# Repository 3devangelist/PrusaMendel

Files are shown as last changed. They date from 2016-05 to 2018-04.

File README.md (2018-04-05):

WARNING: This file is a work in progress and may contain one or two orthographic errors... or maybe more!

# maZEmendel

<p align="center">
  
</p>

I have made this because I can, and i love history! and is a historic printer!

My motivation is to make a printer with a printer, i have a [*Beethefirst+*](https://beeverycreative.com/beethefirstplus/), that is **portable** and **user friendly** and I wanted to prove that with a Little machine, I could create a bigger one! and more maker oriented.
That is the base of REPRAP movement!

You will have all the gcode already generated to print one just like mine in you beethefirst! and if you do, **Show me!**

## First technical notes about this printer

This printer is not easy to assemble, It has a lot of bolts and hardware, but if well assembled, it can be reliable.
You have a calibration paragraph, as a guide for you to calibrate the perpendicularity of the X,Y and Z axis.
I have printed the majority of the parts in PETG because my BTF+ (beeverycreatrive printer) prints it very well, it is more flexible than PLA, thus absorbs some vibrations and has better layer adhesion.

**Side note** if you use PETG, try to use one that is transparent, the opaque ones normally has worse strength proprieties.

## Modeling
I have used **BLENDER**, because I'am a blender hardcore-user, because I can, and because it's really good to edit meshes.

To cut pieces, I have used Rhino, because it's the only paid CAD program i have, but you can use the dxf files, or send me a mail for me to convert the files to your format. To bee fair the only part you have to cut with precision is the Y wood base, later on, i will post the fabrication manual.

The file as called *"maise.blend"*, with that file i have rendered all images for the manual, and modeled all parts that I need to create or change for this build. If you need to edit it, you can and you should! That is the purpose of sharing the code. All the parts have the same name of the BOM file, and are distributed by layers, I know that it could be better organized, but better done than perfect.
You should use some add-on's like "3d print toolbox", "Layer management", "cycle engine", when you use models from blender you can try to clean all the mesh to be printable, but that is normally for power users, and when you use Boolean tools is impossible to make that without losing the modifiers stack, and we have to source the more editable parts we can, for others to be able to change. The pipe-line I use is export meshes to stl with "3d print toolbox" add on, then I use a tool that came with windows10 called "3d Builder" that is great to correct the meshes.

### Correcting meshes on 3d Builder

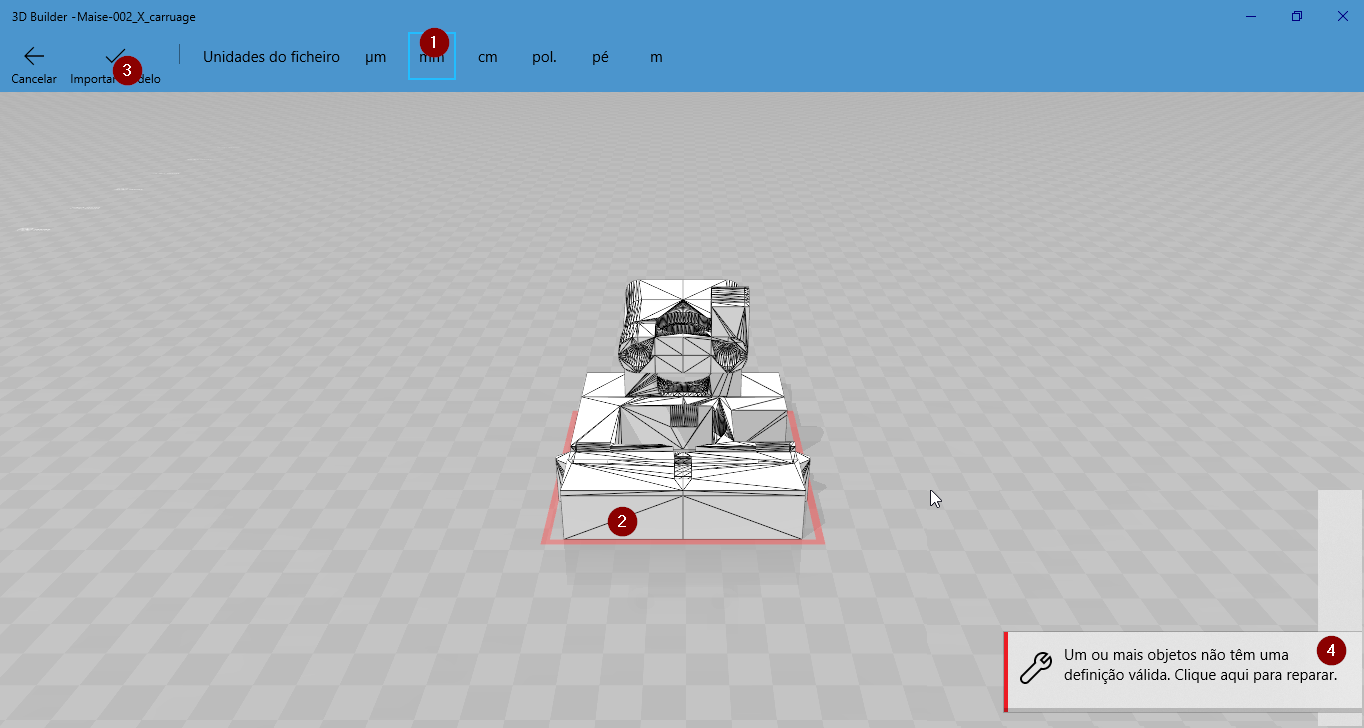
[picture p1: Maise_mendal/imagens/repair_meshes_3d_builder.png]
image 3d builder - heal meshes


- 1 Import as mm;
- 2 A red rectangle in the base of the model, means that the model has errors;
- 3 Import the model;
- 4 When you import the model, a rectangle shows up in the right down of your screen, click on it to repair;
- 5 Save your file em STL;

## Changes

- New X axes;
- remodeled Y;
- Some updates on Z;
- Bowden for extruder;
- E3d v6 hotend;
- Igus sliders for X and Y;
- board MKSgen 1.4;
- Drivers X, Y, E, Trynamic 2100, Z LV8729;
- Added LEDs to the system, you can add RGB "if you do show it!"

Working..

## BOM Build of Materials

[Spreedsheet](https://docs.google.com/spreadsheets/d/16tOSJMvPqgqwrDMo-RX5avmmjWwADpJSkYPEsrkDC4U/edit?usp=sharing)
(only parts to be printed the parts to buy needs to be updated)

## 1. Assembly the Printer

### 1.1. Structure
montage

1. Pick 6X380 M8 rods, and 2X *"001 bar-clamp-tall"*, and M8 Bolts and Washers, and displace them like in the picture.
2. Pick parts: **4X** *"001 Frame vertex with foot"*; **2X** *"001 frame-vertex"*, and assemble 2 strutures like on the image, tighten the nuts by hand. 
3. Pick 6X M8x40 Bolts and assemble like picture, to make shore that the frame will be the most simetric possible, like picture 4. then you can tighten a Little bit before brake, all the nuts.
4. The continuing of picture 3.
5. Pick the M8 Rods like is in the picture, and pick the **6X** *"001 bar-clamp"*, and assemble properly.
6. Assemble the main structure, by hand;

### 1.2. Y Axes

waiting for update

### 1.3. X Axes

waiting for update

### 1.4. Extruder

#### 1.4.1 Saintflint

<p align="center">
  
</p>

This is the best bowden printed extruder I have used! It was developed by a great friend [Michael Memeteau](https://incompreendido/in/mmemetea/), creative and resourceful engineer.
This extruder has a concept that double the area of contact between the motor gear and the filament.
I have edited the model to fit a MK10 type of gear if you have diferent requirements, feel free to edit, you have an editable file [onshape instance](https://cad.onshape.com/documents/5c209690b10748338481382a/w/6d6638f54420d7c76fe7949d/e/2d47f4694787414fab59244e)

In the [source](https://www.thingiverse.com/thing:979113) you have all information you need to assemble the extruder!

**Recommendation** - print all the parts in PETg and 90% infill, it takes longer, uses more plastic but it makes sure you din't end up with a broken extruder.

### 1.5. Hotend
I have used a Bowden setup with E3d v6 Chinese clone, before all the test I am thinking about upgrading it to an original one!

### 1.6. MKS GEN 1.4

I have chosen this because it has a good value for the money, in the BOM you have links to buy the board, Since I want a silent machine I decided to use the TMC2100 stepper drivers for the X, Y and E axis. They are not cheep but they are worth it!
You should be able to assemble the controller with these [instructions](http://reprap.org/wiki/MKS_GEN) from reprap community, if you use LEDs you should connect to the 12V output, the same place you connect the hotend fan.

#### 1.6.1. Assemble models with electronics

waiting for update

### 1.7. ATX Power supply 
To use a PC ATX power supply, you have to convert it, go to this [instructables](http://www.instructables.com/id/A-Makers-Guide-to-ATX-Power-Supplies/) you only need the 12V track, unless you config a raspberrypi with octaprint, if you do, use the 5x track to power the raspberrypi.

### 1.9 Filament Sensor

To implement!

## Firmware _**(Fernando to review)**_

I have a Firmware that you can use [here](https://github.com/3devangelist/PrusaMendel/tree/master/Maise_mendal/Firmware), if you want to configure yourself these Topic you should be able to implement with these [resources](http://marlinfw.org/docs/configuration/configuration.html).
For Base of the firmware i have on git, i have used the Marlin with the hephestos config files, and then edit it them.

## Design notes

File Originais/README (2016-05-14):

Prusa Mendel iteration 2

This is second big change, formerly known as felt branch.
Released 11.11.11 :-)

Please read http://reprap.org/wiki/Prusa_Mendel before attempting to build this. There is also PDF (manual-wiki) with backup documentation from reprap.org.  

Imported stuff:
Extruder by Greg Frost
Parametric Involute Bevel and Spur Gears by GregFrost
Belt pulley is http://www.thingiverse.com/thing:3104 by GilesBathgate

Prusa Mendel part list:

To print (not including the extruder drive):

4x frame-vertex-with-foot
2x frame-vertex-without-foot
2x coupling
1x x-carriage
1x x-end-idler
1x x-end-motor
2x z-motor-mount
4x belt-clamp
2x belt-clamp-nut-holder
8x bar-clamp
2x rod-clamp
1x y-motor-bracket
3x y-bushing
3x endstop-holder

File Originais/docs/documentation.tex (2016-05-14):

\documentclass[11pt]{article}
\usepackage[latin2]{inputenc}
\usepackage{a4wide}
\usepackage{graphicx}
\usepackage{hyperref}
\hypersetup{colorlinks=true,linkcolor=blue}
\title{Prusa Mendel iteration 2 Documentation}
\author{ThingDoc}

\begin{document}

\maketitle
\begin{center}
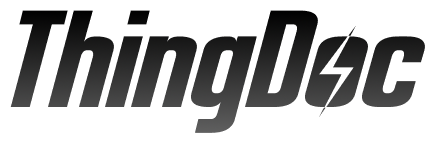
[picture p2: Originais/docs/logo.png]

\end{center}
Prusa Mendel is simplified version of Mendel form RepRap project. RepRap is open source 3D printer.

\newpage

\tableofcontents

\newpage

\section{Bill of Materials}
List of things you need to build the machine divided by categories.

\subsection{Rods and Bars}
\begin{itemize}
\item 1x \hyperlink{thing_idler-m8-piece}{Idler}
\end{itemize}

\subsection{Nuts\&bolts}
\begin{itemize}
\item 3x 608 skate bearing
\item 4x M4 nut
\item 3x M3 10mm screw
\item 2x M4 25mm screw
\item 1x \hyperlink{thing_hobbed-bolt}{M8 hobbed bolt}
\item 8x M3 15mm screw with HEX head
\item 2x M3 10mm screw with hex head
\item 1x M3 25mm screw
\item 1x M3 grub screw
\item 2x M3 25mm screw with HEX head
\item 12x M3 nut
\item 73x M8 washer
\item 74x M8 nut
\item 29x M3 washer
\item 1x M3 10mm screw with flat head
\item 2x M3 40mm screw
\end{itemize}

\subsection{Printed}
\begin{itemize}
\item 1x \hyperlink{thing_extruder-body}{Extruder body}
\item 8x \hyperlink{thing_bar-clamp}{Bar clamp}
\item 4x \hyperlink{thing_y-bushing}{Y bushing}
\item 2x \hyperlink{thing_frame-vertex}{Frame vertex}
\item 1x \hyperlink{thing_large-gear}{Large extruder gear}
\item 1x \hyperlink{thing_small-gear}{Small extruder gear}
\item 2x \hyperlink{thing_rod-clamp}{Rod clamp}
\item 4x \hyperlink{thing_frame-vertex-foot}{Frame vertex with foot}
\item 1x \hyperlink{thing_y-motor-bracket}{Y motor bracket}
\item 2x \hyperlink{thing_belt-clamp}{Belt clamp}
\item 1x \hyperlink{thing_x-carriage}{X carriage}
\item 1x \hyperlink{thing_z-motor-mount}{Z motor mount}
\item 1x \hyperlink{thing_idler}{Extruder Idler}
\end{itemize}

\newpage

\section{Things Overview}
List of things and their descriptions.

\hypertarget{thing_coupling-tube}{\subsection{Coupling tube}}
20mm long piece of PVC tube. 5mm inside diameter, 8mm outside diameter.

\hypertarget{thing_frame-triangle}{\subsection{Frame triangle}}
Two triangle parts which will later form a frame.

\hypertarget{thing_frame-with-axes}{\subsection{Frame with axes}}
Frame with all axes mounted

\hypertarget{thing_frame-vertex}{\subsection{Frame vertex}}
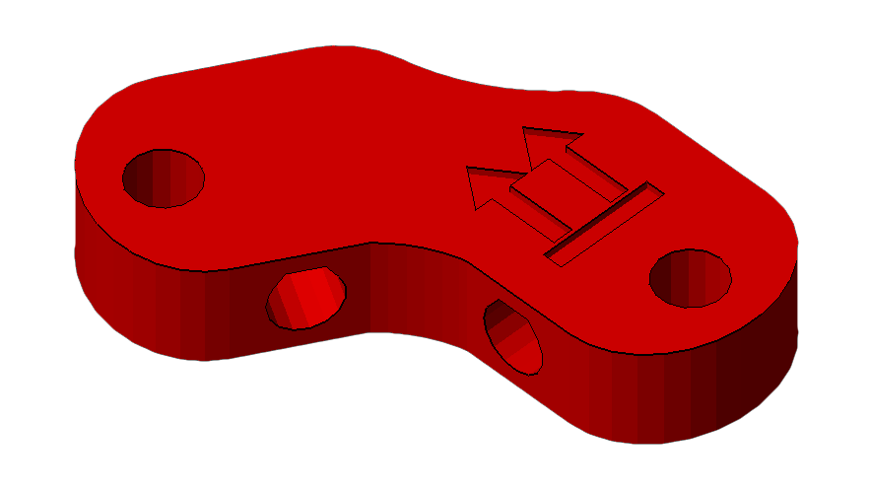
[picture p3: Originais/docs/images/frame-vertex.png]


\hypertarget{thing_frame}{\subsection{Frame}}
Frame for adding all of the other parts
There is a triangle on each side of the Prusa RepRap. You will need to make two of these and then connect them together (in the next steps) to form the Prusa frame. Each side is an equilateral triangle with a frame vertex on each corner. You can use either footed or non-footed vertices to build this. (The footed ones look better, but are not critical.) The instructions assume you are using footed vertices.

\hypertarget{thing_y-motor-bracket}{\subsection{Y motor bracket}}
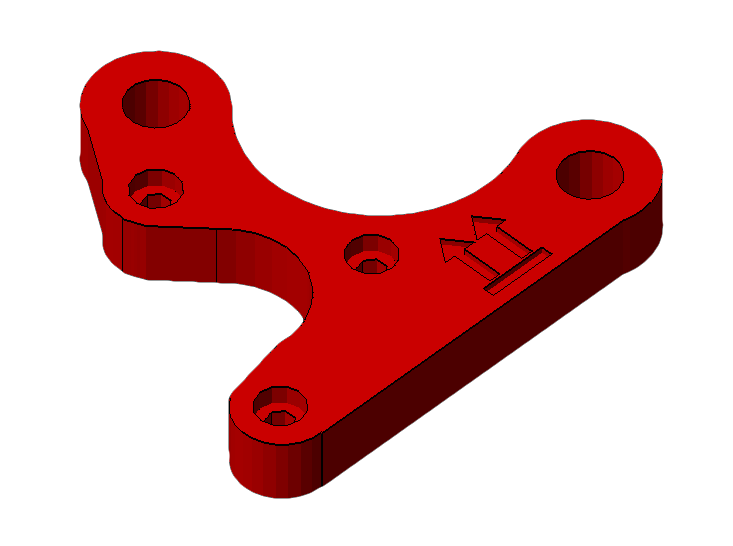
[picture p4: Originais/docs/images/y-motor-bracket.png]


\hypertarget{thing_belt-clamp}{\subsection{Belt clamp}}
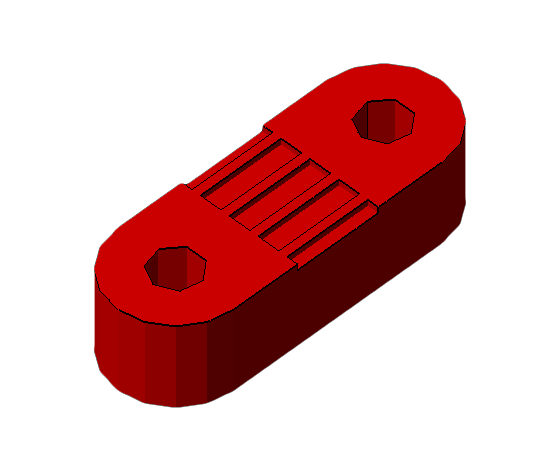
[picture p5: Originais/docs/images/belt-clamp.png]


\hypertarget{thing_hobbed-bolt}{\subsection{M8 hobbed bolt}}

\hypertarget{thing_idler}{\subsection{Extruder Idler}}
Extruder idler

\hypertarget{thing_frame-with-y}{\subsection{Frame with Y axis}}
Frame with Y axis mounted

\hypertarget{thing_y-bushing}{\subsection{Y bushing}}

\hypertarget{thing_large-gear-assembly}{\subsection{Large extruder gear assembly}}

\hypertarget{thing_bar-clamp}{\subsection{Bar clamp}}
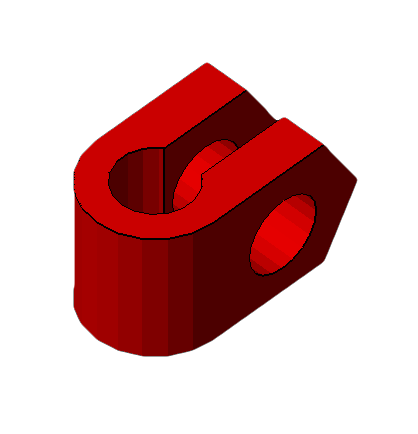
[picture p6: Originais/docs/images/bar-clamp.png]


\hypertarget{thing_xz-axis}{\subsection{XZ axis}}
Assembled XZ axis

\hypertarget{thing_large-gear}{\subsection{Large extruder gear}}

\hypertarget{thing_frame-vertex-foot}{\subsection{Frame vertex with foot}}
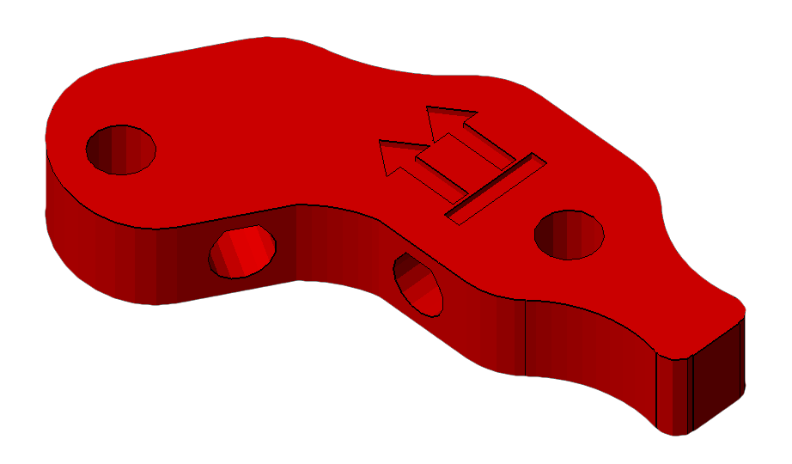
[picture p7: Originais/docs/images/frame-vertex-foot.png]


\hypertarget{thing_x-end-motor}{\subsection{X end motor}}

\hypertarget{thing_extruder-body}{\subsection{Extruder body}}
Extruder body

\hypertarget{thing_small-gear}{\subsection{Small extruder gear}}

\hypertarget{thing_extruder-spring}{\subsection{Extruder spring}}
Spring used for idler on extruder.

\hypertarget{thing_printable-bushing}{\subsection{Printable Bushing}}

\hypertarget{thing_x-carriage}{\subsection{X carriage}}
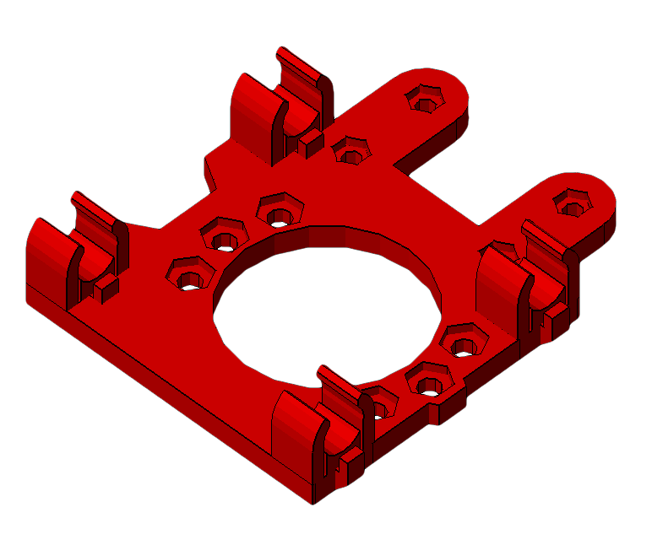
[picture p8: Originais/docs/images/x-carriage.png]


\hypertarget{thing_x-end-idler}{\subsection{X end idler}}

\hypertarget{thing_rod-clamp}{\subsection{Rod clamp}}
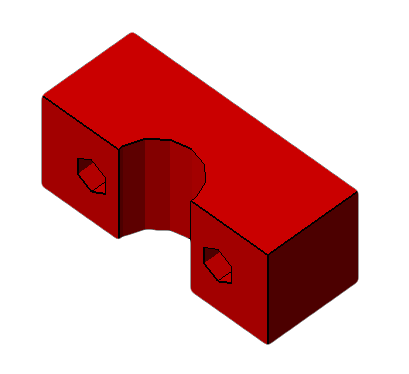
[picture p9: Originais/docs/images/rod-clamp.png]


\hypertarget{thing_z-motor-mount}{\subsection{Z motor mount}}
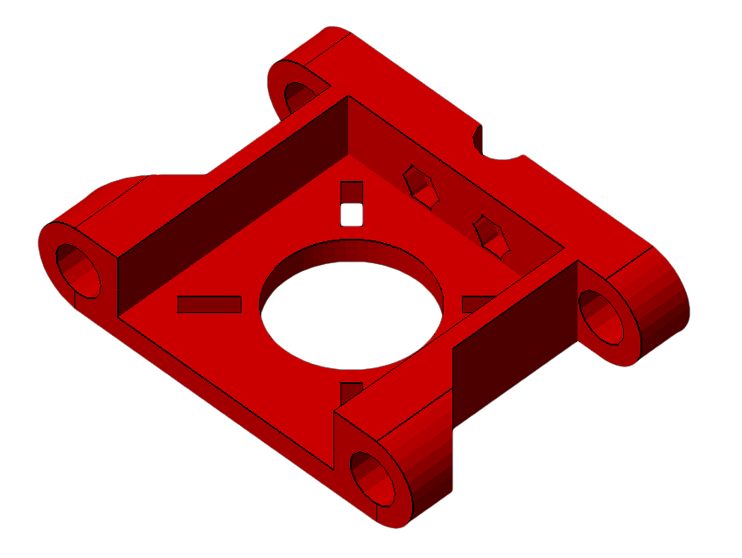
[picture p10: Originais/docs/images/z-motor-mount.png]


\hypertarget{thing_endstop-holder}{\subsection{Endstop holder}}

\hypertarget{thing_bushing}{\subsection{Bushing}}

\hypertarget{thing_idler-m8-piece}{\subsection{Idler}}
Small M8 rod

\hypertarget{thing_pulley}{\subsection{Pulley}}

\hypertarget{thing_coupling}{\subsection{Coupling}}

\hypertarget{thing_y-axis}{\subsection{Y axis}}
Assembled Y axis

\hypertarget{thing_bearing-guide}{\subsection{Bearing guide}}
Helps to hold belt aligned on the bearing.

\hypertarget{thing_cleaned-extruder-body}{\subsection{Clenaed xtruder body}}
Cleaned extruder body

\hypertarget{thing_carriage}{\subsection{Carriage}}
X-carriage with mounted extruder

\hypertarget{thing_extruder}{\subsection{Extruder}}
Extruder

\newpage

\section{Assembly Instructions}

\subsection{Assemble M8 hobbed bolt}Steps:
\begin{enumerate}
\item Use thread cutting bit in electric screwdriver ...
\end{enumerate}

\subsection{Assemble Large extruder gear assembly}
Things needed:
\begin{itemize}
\item 1x \hyperlink{thing_large-gear}{Large extruder gear}
\item 1x \hyperlink{thing_hobbed-bolt}{M8 hobbed bolt}
\end{itemize}
Steps:
\begin{enumerate}
\item Insert hobbed bolt into main hole.
\item Add some M8 washers from other side, later with their count you adjust position of hobbed part in filament path.
\end{enumerate}

\subsection{Assemble Small extruder gear}
Things needed:
\begin{itemize}
\item 1x M3 nut
\item 1x M3 grub screw
\end{itemize}
Steps:
\begin{enumerate}
\item Insert nut into cavity in printed gear.
\item Tighten the grub screw a bit, just to hold in place.
\end{enumerate}

\subsection{Assemble Clenaed xtruder body}
Things needed:
\begin{itemize}
\item 1x \hyperlink{thing_extruder-body}{Extruder body}
\end{itemize}
Steps:
\begin{enumerate}
\item Clean all the supports from the part.
\item One blocks the hole in the middle of the axis and one supports the part later making hinge for idler.
\end{enumerate}

\subsection{Assemble Extruder Idler}
Things needed:
\begin{itemize}
\item 1x 608 skate bearing
\item 1x \hyperlink{thing_idler-m8-piece}{Idler}
\end{itemize}
Steps:
\begin{enumerate}
\item Insert piece of M8 rod into bearing.
\item Insert 608 bearing with rod into printed idler part.
\end{enumerate}

\subsection{Assemble Extruder}
Things needed:
\begin{itemize}
\item 2x 608 skate bearing
\item 2x M4 nut
\item 3x M3 10mm screw
\item 1x \hyperlink{thing_large-gear-assembly}{Large extruder gear assembly}
\item 1x NEMA17 stepper motor
\item 1x \hyperlink{thing_small-gear}{Small extruder gear}
\item 1x \hyperlink{thing_cleaned-extruder-body}{Clenaed xtruder body}
\item 2x M3 40mm screw
\item 8x M3 washer
\item 1x M8 washer
\item 1x \hyperlink{thing_idler}{Extruder Idler}
\item 1x M3 nut
\item 1x M3 25mm screw
\item 2x \hyperlink{thing_extruder-spring}{Extruder spring}
\item 2x M8 nut
\end{itemize}
Steps:
\begin{enumerate}
\item Take idler and insert nut into small nut-trap inside the hinge.
\item While holding the nut in place, preprare M3x25 bolt with washer and screw it into the hinge just enough to hold the nut.
\item Now take the extruder body and idler. Place idler on the hinge counterpart and compleately screw the M3x25 bolt. This will create secured hinge.
\item Place M4 nuts into their nut traps, secure them with piece of tape. We need them in place, since later they would be harder to access.
\item Prepare your NEMA17 stepper motor and three M3x10 screws with washers.
\item Hold motor on place and lightly tighten the screws. We need to adjust motor position later, no need to tighten it hard.
\item Place two skate bearings on ther position, they should snuggly fit in.
\item Insert prepared large gear into the body with mounted bearings.
\item Check if the alignment of hobbed part with the filament path. Adjust it accordingly with adding or removing M8 washers.
\item After adjusting, we need to fix the bolt in. So we place washer at the end of hobbed bolt and with two M8 nuts we will do locknut by tightening them against each other.
\item Check if large gear turns freely.
\item Prepare two M3x40 screws with sandwitch of washer-spring-washer.
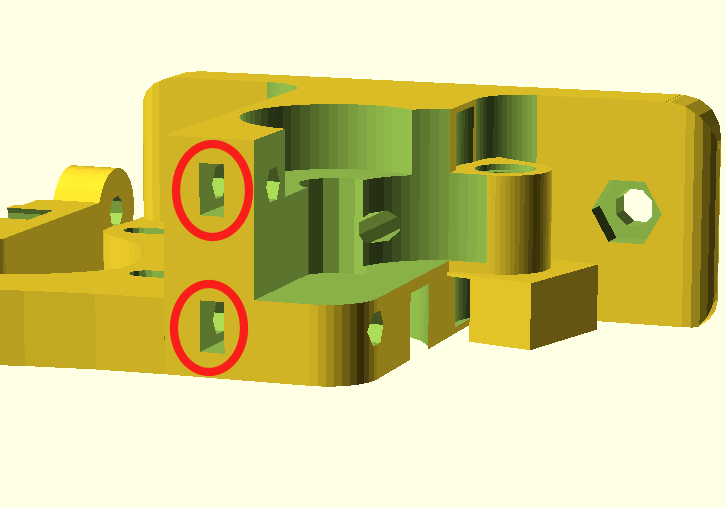
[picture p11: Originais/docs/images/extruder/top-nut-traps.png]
\item Insert two M3 nuts into nut traps on top of drive mechanism.\\ 
\item Insert prepared screws into the holes on idler. Close the idler and tighten the screws into the trapped nuts. More you tighten those screws, more pressure will be on fillament.
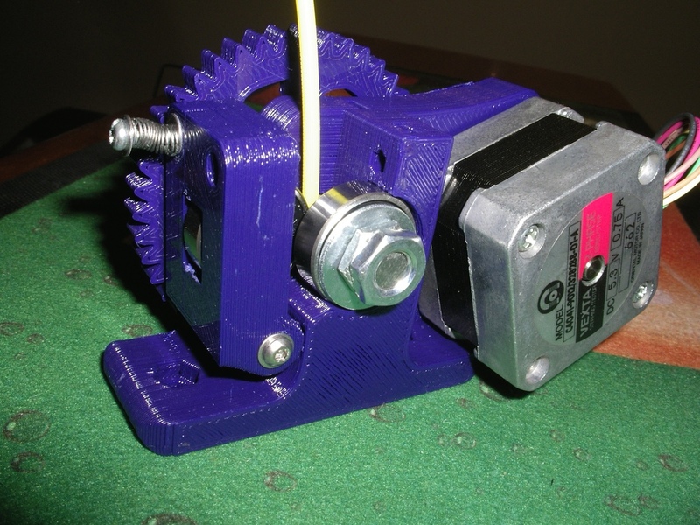
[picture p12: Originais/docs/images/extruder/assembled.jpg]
\item Your extruder is done.\\ 
\end{enumerate}

\subsection{Assemble Frame triangle}
Things needed:
\begin{itemize}
\item 1x \hyperlink{thing_bar-clamp}{Bar clamp}
\item 1x \hyperlink{thing_frame-vertex}{Frame vertex}
\item 2x \hyperlink{thing_frame-vertex-foot}{Frame vertex with foot}
\end{itemize}
Steps:
\begin{enumerate}
\item Take one of the 370mm threaded rods, and slip an M8 washer onto the middle of it.
\item Take the RP bar clamp (the U-shaped bit with the two holes) and slide the threaded rod through the two holes until the clamp sits next to the washer.
\item Slide another washer onto the rod from the other side.
\item Thread two M8 nuts onto either side of the clamp, until they are next to the washer, but do not tighten them yet.
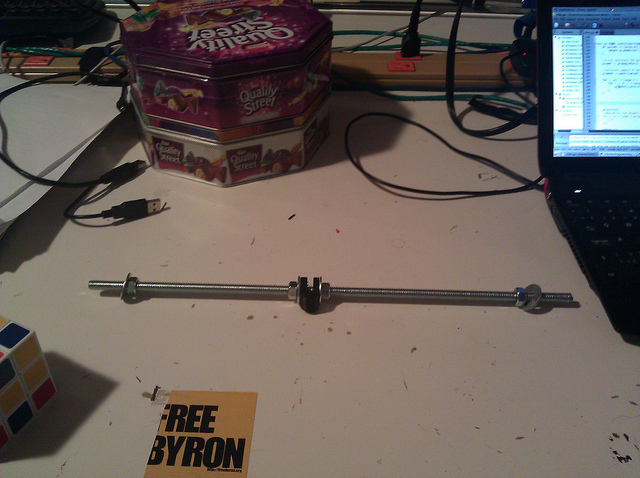
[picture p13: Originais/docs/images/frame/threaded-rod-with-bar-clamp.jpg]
\item Thread another two nuts on each side of the rod, followed by washers. See the picture for what it should look like.\\ 
\item The bar clamp on the threaded rod.
\item Slide the rod through the wider bottom (footed) side of two vertices. Make sure the feet point in the same direction, and the bulge on the non-footed sides of the vertices point outwards.
\item Place another washer and nut on the other side of the vertex. Tighten, but not too much. We'll need a bit of flexibility here still.
\item Take another 370mm M8 threaded rod and place a nut followed by a washer at each end.
\item Place one end of the threaded rod into the one of the two footed frame vertices. It should be in the same plane as the first threaded rod. Fix it in place with a washer and nut. You should now have two sides of the equilateral triangle.
\item Take the third piece of threaded rod and put a nut and washer on each end. Place it in the other footed vertex and fix it in place with a washer and nut. You should now have a triangle of threaded rods with two footed vertices on two of the corners, nothing in the third corner, and a bar clamp between the two vertices.
\item Take the third vertex (non-footed) and slide it onto the threaded rods in the final corner of the triangle.
\item Move all the nuts on the end of the rods to the exact end of the rod. Tighten all the inner nuts. This way, no measurement is needed.
\item You should now have a sturdy triangle with equal-length sides, two feet on the bottom, and a bar clamp between the feet. Adjust the nuts around the bar clamp (but do not crush the bar clamp together yet) until it's approximately in the middle of the rod. Leave the nuts there loose. See the photo for what you should have at this point.
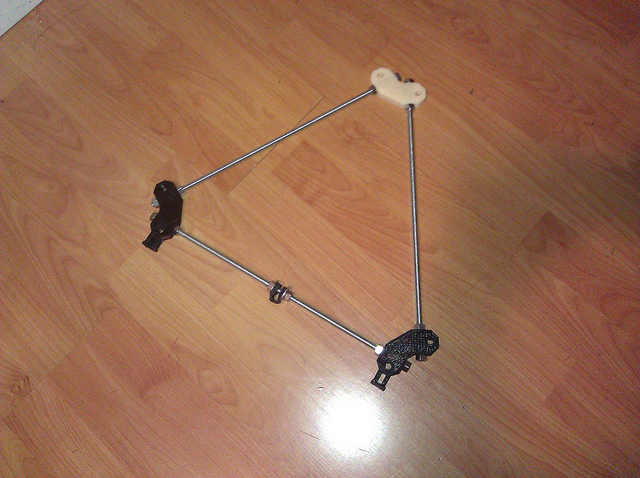
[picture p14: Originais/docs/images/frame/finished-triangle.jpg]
\item That's it, that's one of the triangles done. Repeat the entire procedure for the second triangle. It is identical to the first.\\ 
\end{enumerate}

\subsection{Assemble Prusa Mendel iteration 2}
Things needed:
\begin{itemize}
\item 1x \hyperlink{thing_carriage}{Carriage}
\item 1x \hyperlink{thing_frame-with-axes}{Frame with axes}
\end{itemize}
Steps:
\begin{enumerate}
\item Assembly info
\end{enumerate}

\newpage

\end{document}

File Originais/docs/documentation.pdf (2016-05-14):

## Prusa Mendel iteration 2 Documentation

ThingDoc

November 16, 2011

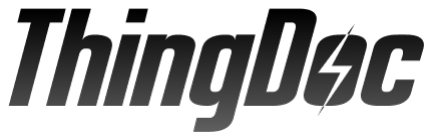
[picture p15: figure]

Prusa Mendel is simplified version of Mendel form RepRap project. RepRap is open source 3D printer.

## Contents

## 1 Bill of Materials

List of things you need to build the machine divided by categories.

### 1.1 Rods and Bars

- 1x Idler

### 1.2 Nuts&bolts

- 3x 608 skate bearing
- 4x M4 nut
- 3x M3 10mm screw
- 2x M4 25mm screw
- 1x M8 hobbed bolt
- 8x M3 15mm screw with HEX head
- 2x M3 10mm screw with hex head
- 1x M3 25mm screw
- 1x M3 grub screw
- 2x M3 25mm screw with HEX head
- 12x M3 nut
- 73x M8 washer
- 74x M8 nut
- 29x M3 washer
- 1x M3 10mm screw with flat head
- 2x M3 40mm screw

### 1.3 Printed

- 1x Extruder body
- 8x Bar clamp
- 4x Y bushing
- 2x Frame vertex
- 1x Y motor bracket
- 1x Small extruder gear

- 2x Rod clamp
- 4x Frame vertex with foot
- 1x Large extruder gear
- 2x Belt clamp
- 1x Extruder Idler
- 1x Z motor mount
- 1x X carriage

## 2 Things Overview

List of things and their descriptions.

### 2.1 Coupling tube

20mm long piece of PVC tube. 5mm inside diameter, 8mm outside diameter.

### 2.2 Frame triangle

Two triangle parts which will later form a frame.

### 2.3 Frame with axes

Frame with all axes mounted

### 2.4 Frame vertex

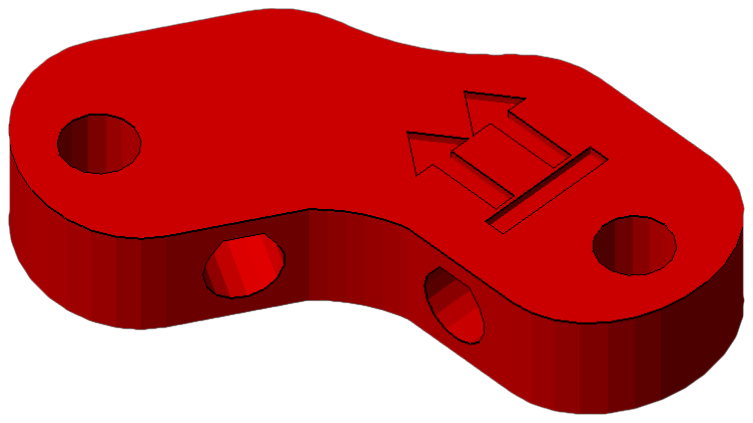
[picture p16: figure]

### 2.5 Frame

Frame for adding all of the other parts There is a triangle on each side of the Prusa RepRap. You will need to make two of these and then connect them together (in the next steps) to form the Prusa frame. Each side is an equilateral triangle with a frame vertex on each corner. You can use either footed or non-footed vertices to build this. (The footed ones look better, but are not critical.) The instructions assume you are using footed vertices.

### 2.6 Y motor bracket

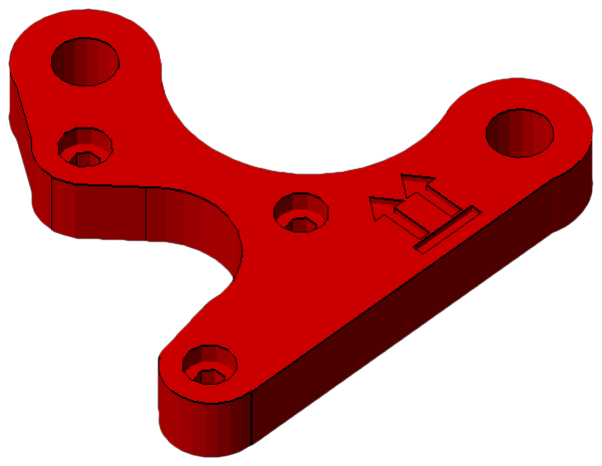
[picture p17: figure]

### 2.7 Belt clamp

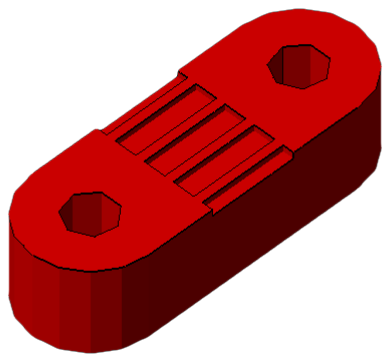
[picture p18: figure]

### 2.8 M8 hobbed bolt

### 2.9 Extruder Idler

Extruder idler

### 2.10 Frame with Y axis

Frame with Y axis mounted

### 2.11 Y bushing

### 2.12 Bar clamp

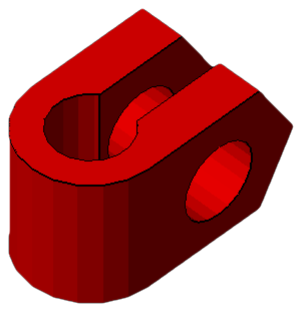
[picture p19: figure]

### 2.13 XZ axis

Assembled XZ axis

### 2.14 Large extruder gear

### 2.15 Frame vertex with foot

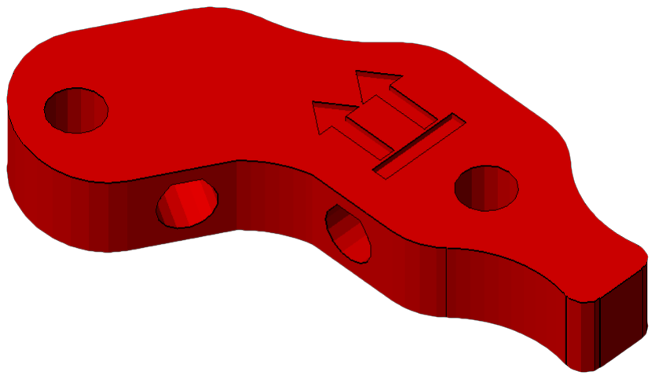
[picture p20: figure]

### 2.16 X end motor

### 2.17 Extruder body

Extruder body

### 2.18 Small extruder gear

### 2.19 Extruder spring

Spring used for idler on extruder.

### 2.20 Printable Bushing

### 2.21 X carriage

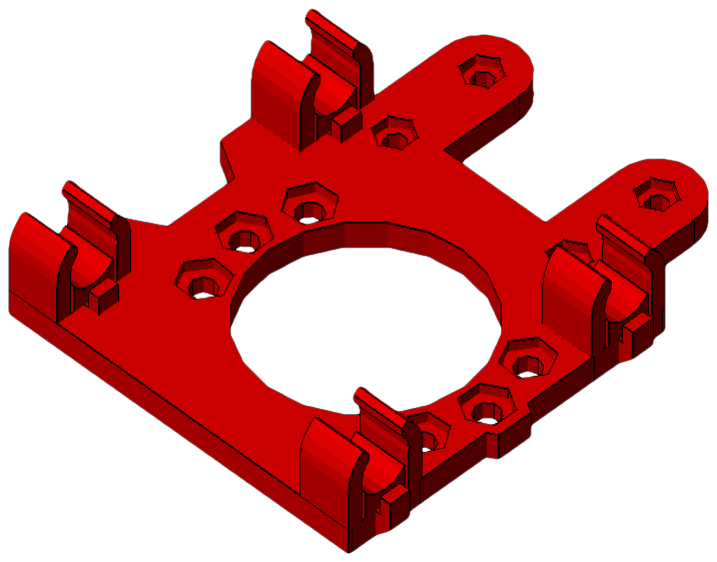
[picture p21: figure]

### 2.22 X end idler

### 2.23 Rod clamp

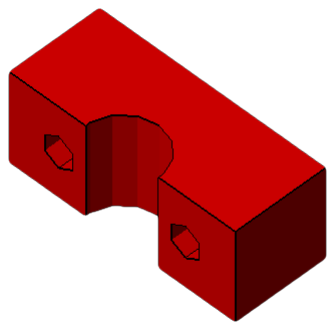
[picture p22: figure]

### 2.24 Z motor mount

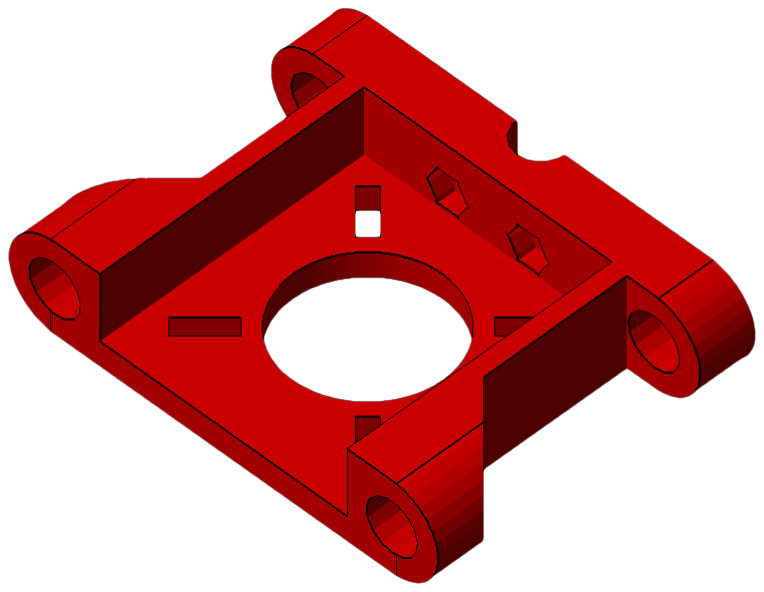
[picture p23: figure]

### 2.25 Endstop holder

### 2.26 Bushing

### 2.27 Idler

Small M8 rod

### 2.28 Pulley

### 2.29 Coupling

### 2.30 Y axis

Assembled Y axis

### 2.31 Bearing guide

Helps to hold belt aligned on the bearing.

### 2.32 Carriage

X-carriage with mounted extruder

### 2.33 Extruder

Extruder

## 3 Assembly Instructions

### 3.1 Assemble Small extruder gear

Things needed:

- 1x M3 nut
- 1x M3 grub screw

Steps:

1. Insert nut into cavity in printed gear.
2. Tighten the grub screw a bit, just to hold in place.

### 3.2 Assemble M8 hobbed bolt

Steps:

1. Use thread cutting bit in electric screwdriver ...

### 3.3 Assemble Large extruder gear

Things needed:

- 1x M8 hobbed bolt

Steps:

1. Insert hobbed bolt into main hole.
2. Add some M8 washers from other side, later with their count you adjust position of hobbed part in filament path.

### 3.4 Assemble Extruder Idler

Things needed:

- 1x 608 skate bearing
- 1x Idler

Steps:

1. Insert piece of M8 rod into bearing.
2. Insert 608 bearing with rod into printed idler part.

### 3.5 Assemble Extruder

Things needed:

- 2x 608 skate bearing
- 1x Extruder body
- 3x M3 10mm screw
- 2x M4 nut
- 1x Small extruder gear
- 1x M3 25mm screw
- 1x NEMA17 stepper motor
- 1x Large extruder gear
- 8x M3 washer
- 1x M8 washer
- 1x Extruder Idler
- 1x M3 nut
- 2x M3 40mm screw
- 2x Extruder spring
- 2x M8 nut

Steps:

1. Take idler and insert nut into small nut-trap inside the hinge.
2. While holding the nut in place, preprare M3x25 bolt with washer and screw it into the hinge just enough to hold the nut.
3. Now take the extruder body and idler. Place idler on the hinge counterpart and com-pleately screw the M3x25 bolt. This will create secured hinge.
4. Place M4 nuts into their nut traps, secure them with piece of tape. We need them in place, since later they would be harder to access.
5. Prepare your NEMA17 stepper motor and three M3x10 screws with washers.
6. Hold motor on place and lightly tighten the screws. We need to adjust motor position later, no need to tighten it hard.
7. Place two skate bearings on ther position, they should snuggly fit in.
8. Insert prepared large gear into the body with mounted bearings.

9. Check if the alignment of hobbed part with the filament path. Adjust it accordingly with adding or removing M8 washers.
10. After adjusting, we need to fix the bolt in. So we place washer at the end of hobbed bolt and with two M8 nuts we will do locknut by tightening them against each other.
11. Check if large gear turns freely.
12. Prepare two M3x40 screws with sandwitch of washer-spring-washer.
13. Insert two M3 nuts into nut traps on top of drive mechanism.


14. Insert prepared screws into the holes on idler. Close the idler and tighten the screws into the trapped nuts. More you tighten those screws, more pressure will be on fillament.
15. Your extruder is done.


### 3.6 Assemble Frame triangle

Things needed:

- 1x Bar clamp
- 1x Frame vertex
- 2x Frame vertex with foot

Steps:

1. Take one of the 370mm threaded rods, and slip an M8 washer onto the middle of it.
2. Take the RP bar clamp (the U-shaped bit with the two holes) and slide the threaded rod through the two holes until the clamp sits next to the washer.
3. Slide another washer onto the rod from the other side.
4. Thread two M8 nuts onto either side of the clamp, until they are next to the washer, but do not tighten them yet.

5. Thread another two nuts on each side of the rod, followed by washers. See the picture for what it should look like.


6. The bar clamp on the threaded rod.
7. Slide the rod through the wider bottom (footed) side of two vertices. Make sure the feet point in the same direction, and the bulge on the non-footed sides of the vertices point outwards.
8. Measure the distance. The distance between the two vertices should be 290mm (along the rod, equivalent is 11-13/32”). Get it approximately right now, we will check this again later. If you have a frame jig, place it between the two vertices and adjust the nuts until you can just barely fit the jig J1 between them.
9. Place another washer and nut on the other side of the vertex. Tighten, but not too much. We’ll need a bit of flexibility here still.
10. Take another 370mm M8 threaded rod and place a nut followed by a washer at each end.
11. Place one end of the threaded rod into the one of the two footed frame vertices. It should be in the same plane as the first threaded rod. Fix it in place with a washer and nut. You should now have two sides of the equilateral triangle.
12. Take the third piece of threaded rod and put a nut and washer on each end. Place it in the other footed vertex and fix it in place with a washer and nut. You should now have a triangle of threaded rods with two footed vertices on two of the corners, nothing in the third corner, and a bar clamp between the two vertices.
13. Take the third vertex (non-footed) and slide it onto the threaded rods in the final corner of the triangle. Measure the lengths of the three sides to make sure they are all 290mm long (along the rod from plastic part to plastic part, equivalent is 11-13/32”). Adjust the nuts to make sure this is so. Use the frame jig J1 if you have one. Once done, place a washer and nut on each of the two rods at the top of the vertex. Tighten all the outer nuts.
14. The finished frame triangle
15. You should now have a sturdy triangle with equal-length sides, two feet on the bottom, and a bar clamp between the feet. Adjust the nuts around the bar clamp (but do not crush the bar clamp together yet) until it’s approximately in the middle of the rod. Leave the nuts there loose. See the photo for what you should have at this point.

16. That’s it, that’s one of the triangles done. Repeat the entire procedure for the second triangle. It is identical to the first.


### 3.7 Assemble Prusa Mendel iteration 2

Things needed:

- 1x Carriage
- 1x Frame with axes

Steps:

1. Assembly info

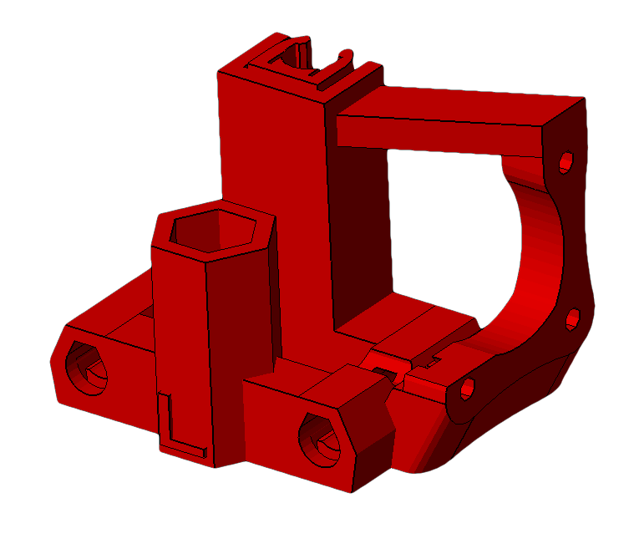
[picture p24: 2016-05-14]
Originais/docs/images/x-end-motor.png

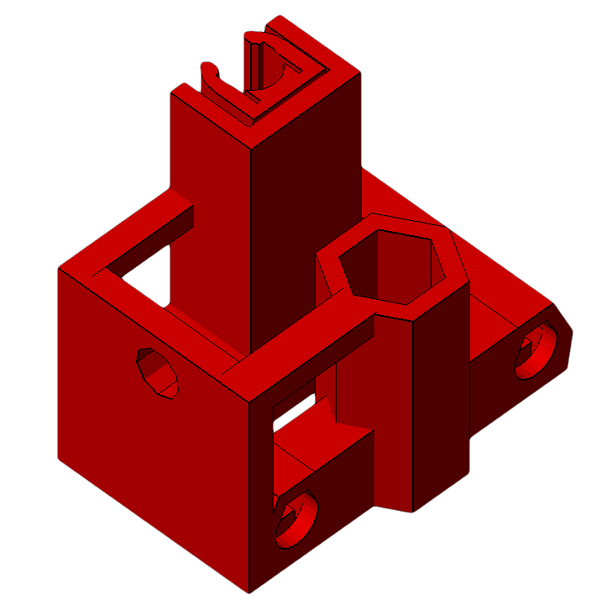
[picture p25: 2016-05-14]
Originais/docs/images/x-end-idler.png

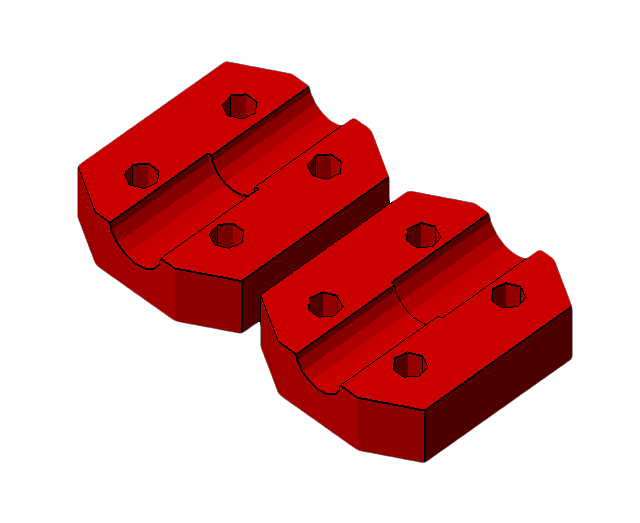
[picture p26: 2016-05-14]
Originais/docs/images/coupling.png

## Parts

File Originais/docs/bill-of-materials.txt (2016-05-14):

Bill of Materials: Prusa Mendel iteration 2
+++++++++++++++++++++++++++++++++++++++++++

Rods and Bars
=============
- 1x Idler 

Nuts&bolts
==========
- 3x 608 skate bearing
- 4x M4 nut
- 3x M3 10mm screw
- 2x M4 25mm screw
- 1x M8 hobbed bolt
- 8x M3 15mm screw with HEX head
- 2x M3 10mm screw with hex head
- 1x M3 25mm screw
- 1x M3 grub screw
- 2x M3 25mm screw with HEX head
- 12x M3 nut
- 73x M8 washer
- 74x M8 nut
- 29x M3 washer
- 1x M3 10mm screw with flat head
- 2x M3 40mm screw

Printed
=======
- 1x Extruder body
- 8x Bar clamp
- 4x Y bushing
- 2x Frame vertex
- 1x Large extruder gear
- 1x Small extruder gear
- 2x Rod clamp
- 4x Frame vertex with foot
- 1x Y motor bracket
- 4x Belt clamp
- 2x Belt clamp nut holder
- 1x X carriage
- 2x Z motor mount
- 1x Extruder Idler
- 2x Coupling
- 3x Endstop holder
- 2x Pulley

----
Generated on 2011/12/03 00:41:02 by ThingDoc - http://thingdoc.org/

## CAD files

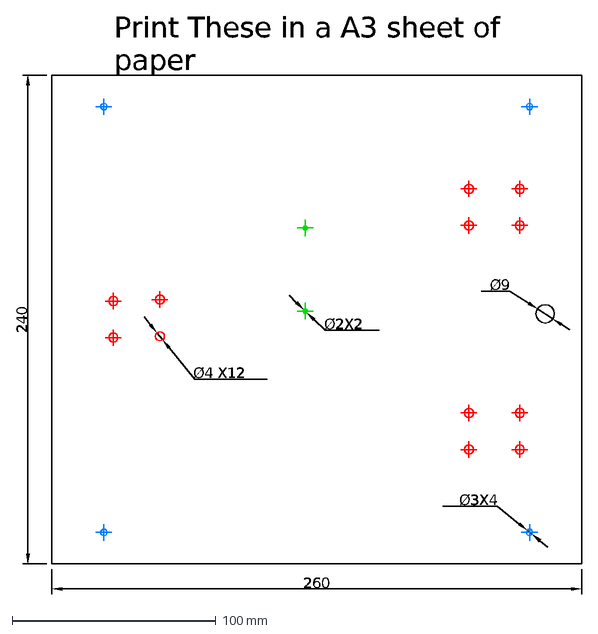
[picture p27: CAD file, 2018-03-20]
Maise_mendal/CUT_FILES/BASE_CUT_WOOD.DXF
Ø3X4
Ø2X2
Ø9
Print These in a A3 sheet of paper
240
260
Ø4 X12

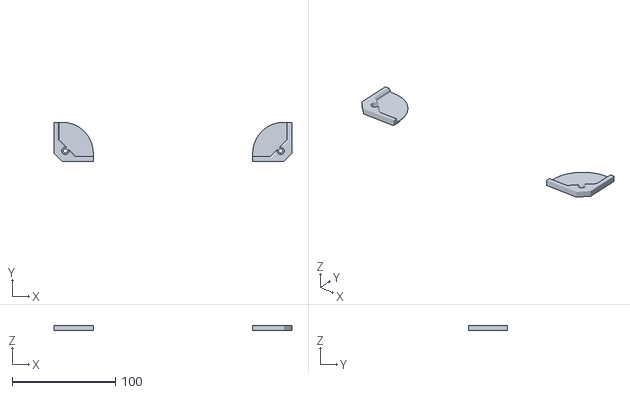
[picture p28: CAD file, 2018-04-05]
Maise_mendal/Maise-001_-_glass_guide_001.stl
230.9 x 38.1 x 4.80

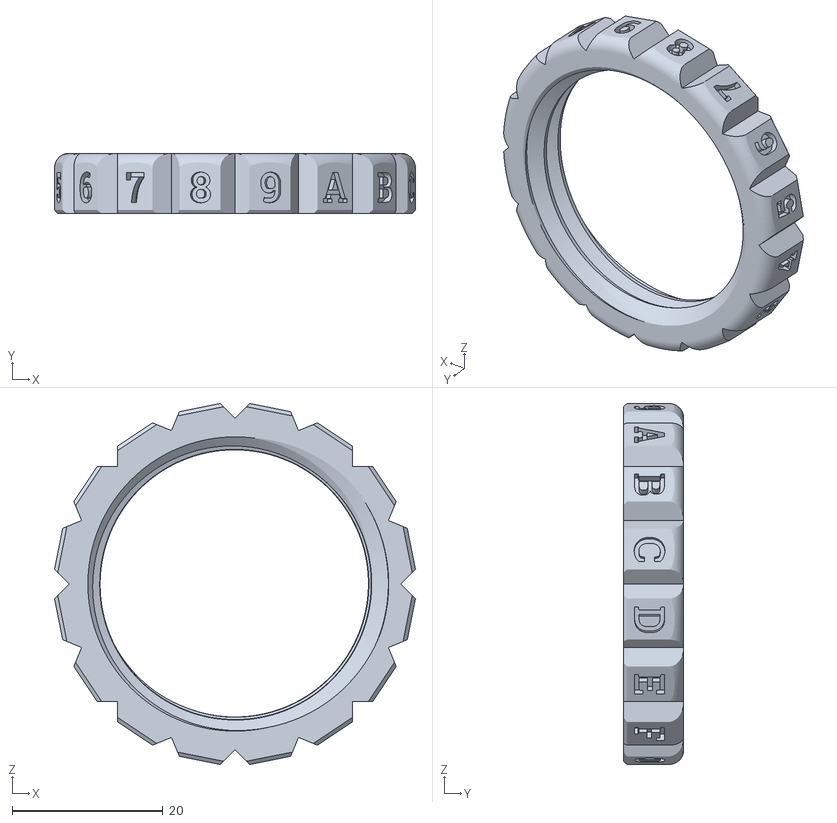
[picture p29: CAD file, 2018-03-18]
Maise_mendal/Saintflint/The Saint - Ring.stl
47.8 x 8.00 x 47.8

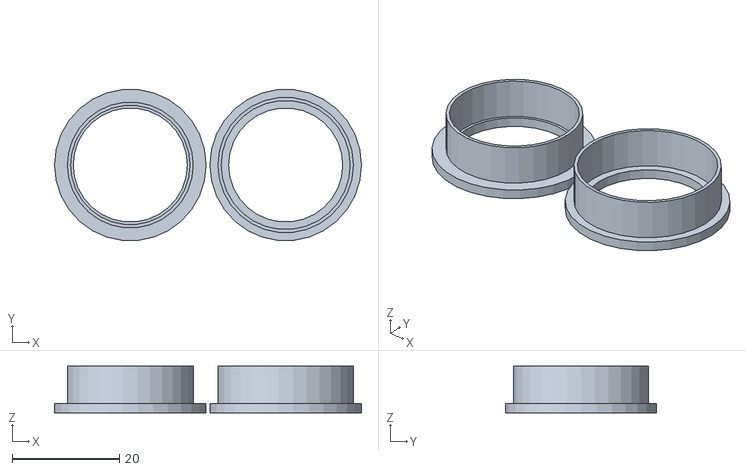
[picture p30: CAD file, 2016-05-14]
Originais/metric-prusa-lm8uu/bearing-guide.stl
57.3 x 28.1 x 8.70

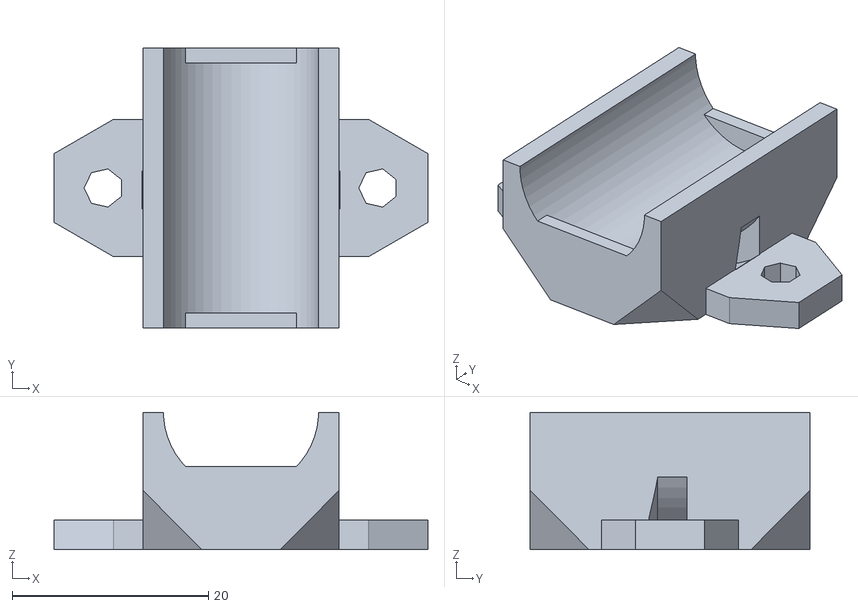
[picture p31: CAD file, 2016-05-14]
Originais/metric-prusa-lme8uu/y-bushing.stl
38.1 x 28.5 x 14.0

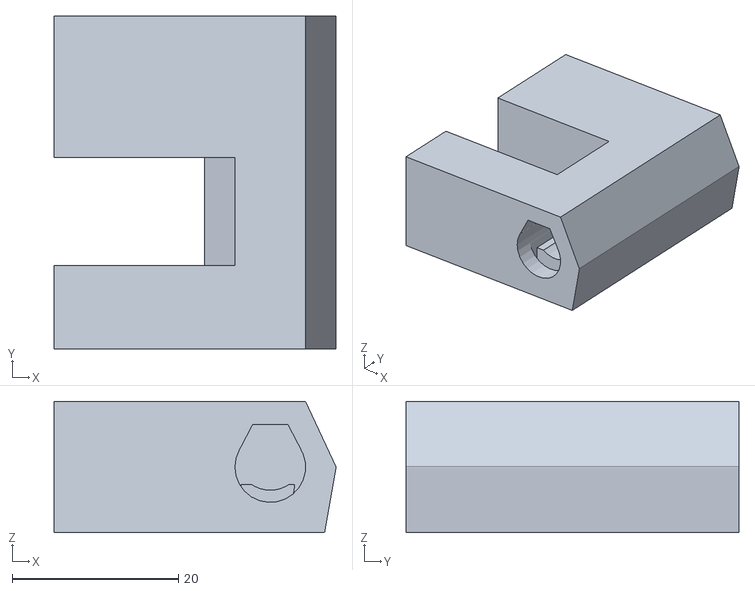
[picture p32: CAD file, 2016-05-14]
Originais/metric-prusa/side test.stl
33.9 x 40.0 x 15.8

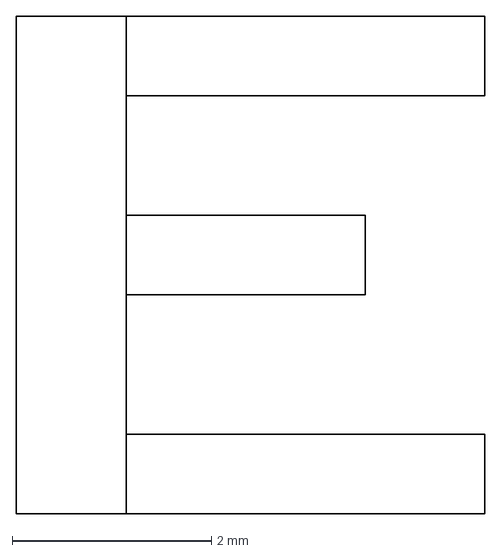
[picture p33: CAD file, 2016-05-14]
Originais/source/this-way-up.dxf
4.70 x 5.00 mm

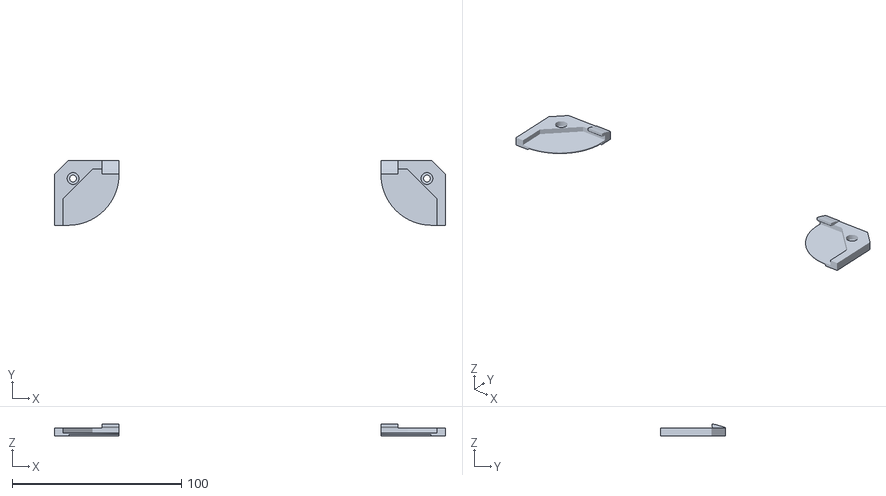
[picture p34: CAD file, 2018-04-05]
Maise_mendal/Maise-001_-_glass_guide.stl
230.9 x 38.1 x 7.30

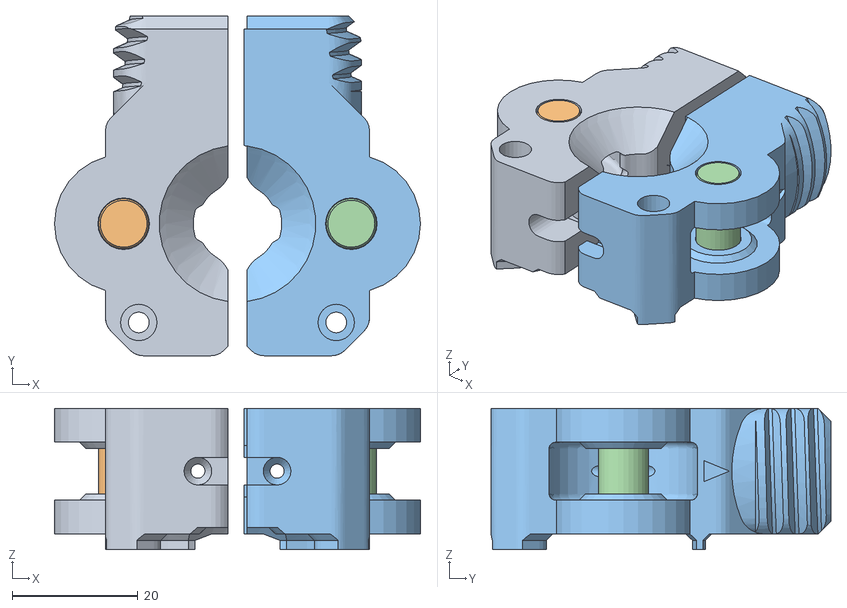
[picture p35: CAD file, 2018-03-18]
Maise_mendal/Saintflint/The Saint.obj
58.2 x 54.0 x 22.5

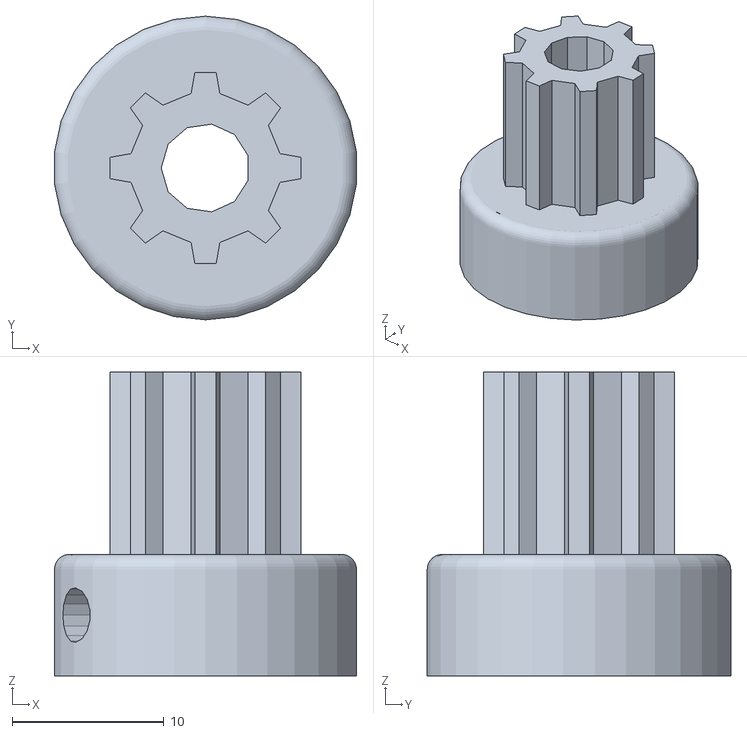
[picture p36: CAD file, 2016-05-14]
Originais/metric-prusa-lme8uu/pulley.stl
19.9 x 20.0 x 20.0

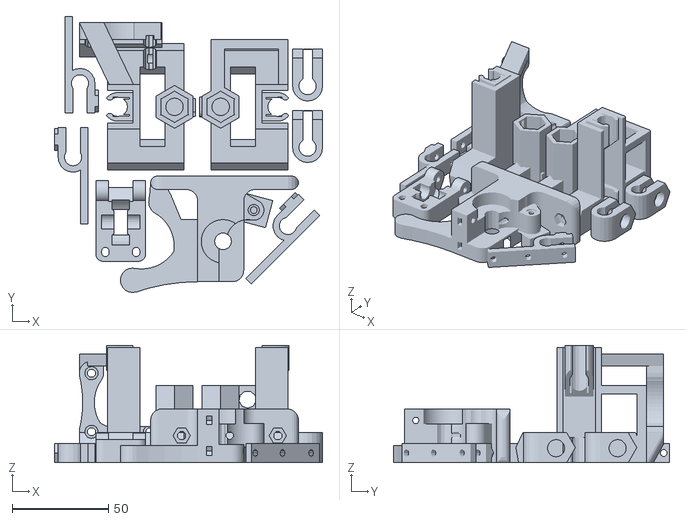
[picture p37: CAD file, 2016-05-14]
Originais/metric-prusa/mendel-plate-1.stl
139.5 x 143.6 x 61.0

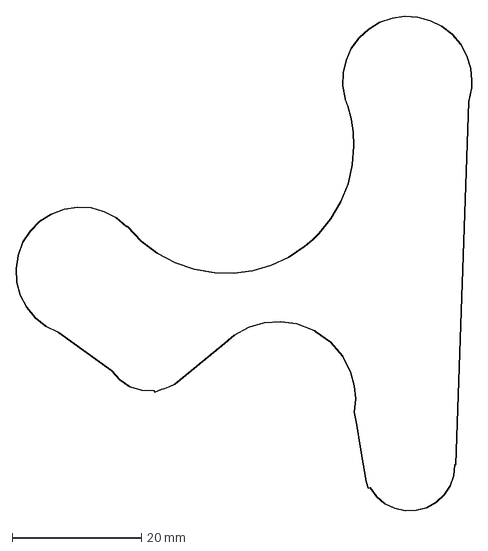
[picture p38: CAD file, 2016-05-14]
Originais/source/ybrac-t.dxf
70.5 x 76.4 mm

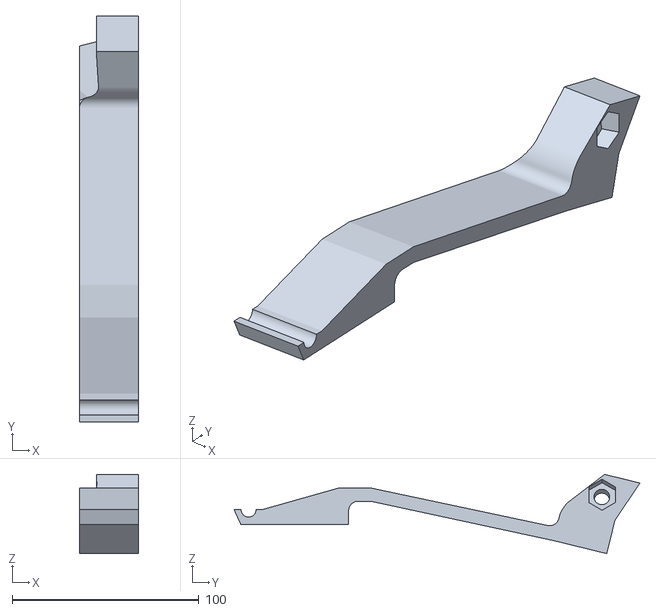
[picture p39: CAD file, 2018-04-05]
Maise_mendal/Maise-001_SPOOLHOLDEr.stl
31.8 x 217.4 x 42.4

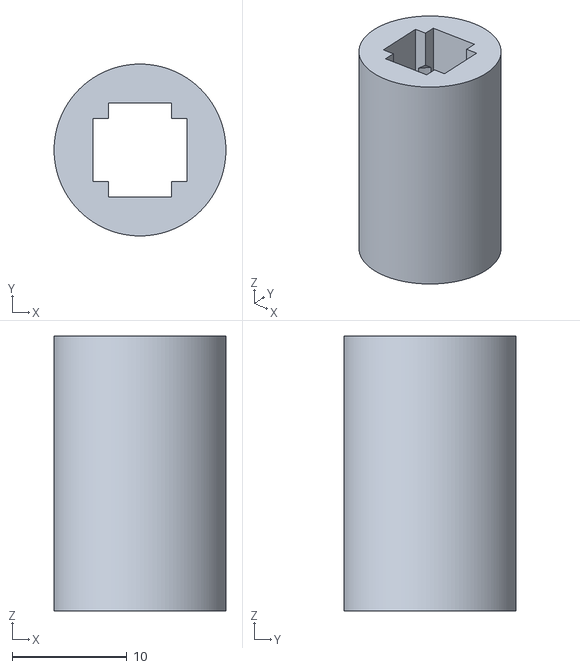
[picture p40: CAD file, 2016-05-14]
Originais/metric-prusa-lm8uu/printable-bushing-lm8uu.stl
15.0 x 15.0 x 24.0

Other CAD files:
Originais/metric-prusa/frame-vertex-foot.stl
Originais/source/bed-drilling.dxf
Maise_mendal/Maise-001_-_support_filament.stl
Originais/source/configuration.scad
Originais/source/inc/parametric_involute_gear_v5.0.scad
Originais/source/x-end-motor.scad
Originais/source/z-motor-mount.scad
Maise_mendal/CUT_FILES/BASE_CUT_WOOD.3dm
Maise_mendal/MKSGEN_BOARD/MKS_GEN1.4Board.blend
Maise_mendal/Maise-002_X_carruage.stl
Maise_mendal/Maise.blend
Maise_mendal/calibration_plate-Base_calibration.stl
Maise_mendal/calibration_plate.blend
Originais/metric-prusa-lm8uu/bar-clamp.stl
Originais/metric-prusa-lm8uu/belt-clamp-nut-holder.stl
Originais/metric-prusa-lm8uu/belt-clamp.stl
Originais/metric-prusa-lm8uu/coupling.stl
Originais/metric-prusa-lm8uu/endstop-holder.stl
Originais/metric-prusa-lm8uu/frame-vertex-foot.stl
Originais/metric-prusa-lm8uu/frame-vertex.stl
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

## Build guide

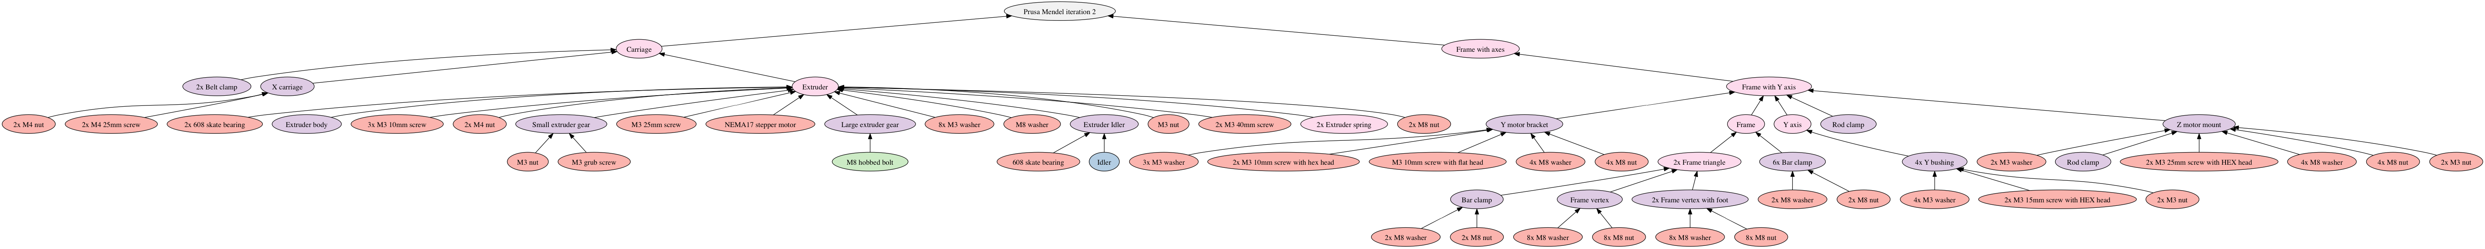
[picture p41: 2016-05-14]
Originais/docs/assembly-graph.png

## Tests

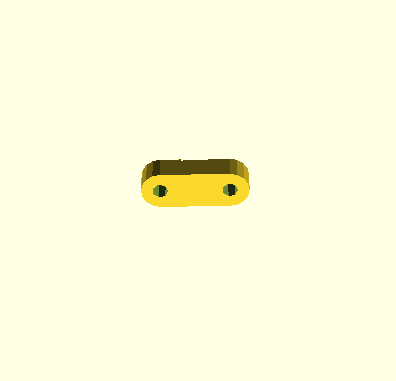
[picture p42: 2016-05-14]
Originais/source/test.png

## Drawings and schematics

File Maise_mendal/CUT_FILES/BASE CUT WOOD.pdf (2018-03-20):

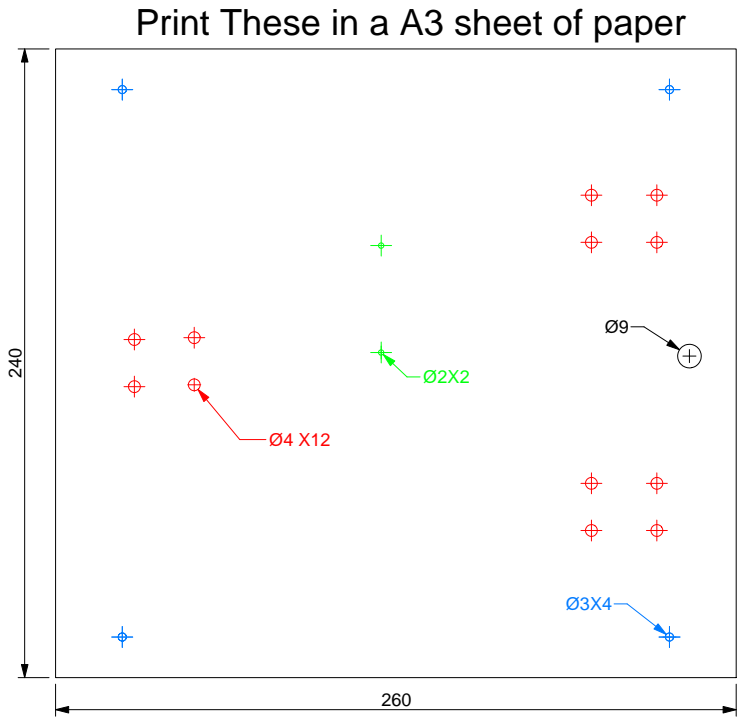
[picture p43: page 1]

Print These in a A3 sheet of paper

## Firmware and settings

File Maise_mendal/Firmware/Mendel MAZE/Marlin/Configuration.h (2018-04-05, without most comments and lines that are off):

#define CONFIGURATION_H
#define CONFIGURATION_H_VERSION 010107
#define STRING_CONFIG_H_AUTHOR "(none, default config)" // Who made the changes.
#define SHOW_BOOTSCREEN
#define STRING_SPLASH_LINE1 SHORT_BUILD_VERSION // will be shown during bootup in line 1
#define STRING_SPLASH_LINE2 WEBSITE_URL         // will be shown during bootup in line 2
#define SERIAL_PORT 0
#define BAUDRATE 115200
  #define MOTHERBOARD BOARD_RAMPS_14_EFB
#define CUSTOM_MACHINE_NAME "Mendel maZE"
#define SOURCE_CODE_URL "https://github.com/3devangelist/PrusaMendel"
#define EXTRUDERS 1
#define DEFAULT_NOMINAL_FILAMENT_DIA 1.75
#define POWER_SUPPLY 1
#define TEMP_SENSOR_0 1
#define TEMP_SENSOR_1 0
#define TEMP_SENSOR_2 0
#define TEMP_SENSOR_3 0
#define TEMP_SENSOR_4 0
#define TEMP_SENSOR_BED 1
#define DUMMY_THERMISTOR_998_VALUE 25
#define DUMMY_THERMISTOR_999_VALUE 100
#define MAX_REDUNDANT_TEMP_SENSOR_DIFF 10
#define TEMP_RESIDENCY_TIME 10  // (seconds)
#define TEMP_HYSTERESIS 8       // (degC) range of +/- temperatures considered "close" to the target one
#define TEMP_WINDOW     0,5       // (degC) Window around target to start the residency timer x degC early.
#define TEMP_BED_RESIDENCY_TIME 0   // (seconds)
#define TEMP_BED_HYSTERESIS 8       // (degC) range of +/- temperatures considered "close" to the target one
#define TEMP_BED_WINDOW     0,5       // (degC) Window around target to start the residency timer x degC early.
#define HEATER_0_MINTEMP 5
#define HEATER_1_MINTEMP 5
#define HEATER_2_MINTEMP 5
#define HEATER_3_MINTEMP 5
#define HEATER_4_MINTEMP 5
#define BED_MINTEMP 5
#define HEATER_0_MAXTEMP 280
#define HEATER_1_MAXTEMP 280
#define HEATER_2_MAXTEMP 280
#define HEATER_3_MAXTEMP 280
#define HEATER_4_MAXTEMP 280
#define BED_MAXTEMP 150
#define PIDTEMP
#define BANG_MAX 255     // Limits current to nozzle while in bang-bang mode; 255=full current
#define PID_MAX BANG_MAX // Limits current to nozzle while PID is active (see PID_FUNCTIONAL_RANGE below); 255=full current
#define PID_K1 0.95      // Smoothing factor within the PID
  #define PID_FUNCTIONAL_RANGE 10 // If the temperature difference between the target temperature and the actual temperature
  #define  DEFAULT_Kp 43.77
  #define  DEFAULT_Ki 8.62
  #define  DEFAULT_Kd 55.58
#define MAX_BED_POWER 255 // limits duty cycle to bed; 255=full current
#define PREVENT_COLD_EXTRUSION
#define EXTRUDE_MINTEMP 170
#define PREVENT_LENGTHY_EXTRUDE
#define EXTRUDE_MAXLENGTH 200
#define USE_XMIN_PLUG
#define USE_YMIN_PLUG
#define USE_ZMIN_PLUG
#define ENDSTOPPULLUPS // Comment this out (using // at the start of the line) to disable the endstop pullup resistors
#define X_MIN_ENDSTOP_INVERTING true  // set to true to invert the logic of the endstop.
#define Y_MIN_ENDSTOP_INVERTING true  // set to true to invert the logic of the endstop.
#define Z_MIN_ENDSTOP_INVERTING true  // set to true to invert the logic of the endstop.
#define X_MAX_ENDSTOP_INVERTING true  // set to true to invert the logic of the endstop.
#define Y_MAX_ENDSTOP_INVERTING true  // set to true to invert the logic of the endstop.
#define Z_MAX_ENDSTOP_INVERTING true  // set to true to invert the logic of the endstop.
#define Z_MIN_PROBE_ENDSTOP_INVERTING true  // set to true to invert the logic of the probe.
#define DEFAULT_AXIS_STEPS_PER_UNIT   { 80, 80, 396.3, 93}
#define DEFAULT_MAX_FEEDRATE          { 200, 200, 20, 80 }
#define DEFAULT_MAX_ACCELERATION      { 500, 500, 10, 500 }
#define DEFAULT_ACCELERATION           650    // X, Y, Z and E acceleration for printing moves
#define DEFAULT_RETRACT_ACCELERATION   500    // E acceleration for retracts
#define DEFAULT_TRAVEL_ACCELERATION   2000    // X, Y, Z acceleration for travel (non printing) moves
#define DEFAULT_XJERK                 30
#define DEFAULT_YJERK                 30
#define DEFAULT_ZJERK                 10
#define DEFAULT_EJERK                 10
#define Z_MIN_PROBE_ENDSTOP
#define X_PROBE_OFFSET_FROM_EXTRUDER -25     // X offset: -left  +right  [of the nozzle]
#define Y_PROBE_OFFSET_FROM_EXTRUDER -29     // Y offset: -front +behind [the nozzle]
#define Z_PROBE_OFFSET_FROM_EXTRUDER -12.35  // Z offset: -below +above  [the nozzle]
#define XY_PROBE_SPEED 8000
#define Z_PROBE_SPEED_FAST HOMING_FEEDRATE_Z
#define Z_PROBE_SPEED_SLOW (Z_PROBE_SPEED_FAST / 2)
#define Z_CLEARANCE_DEPLOY_PROBE   15 // Z Clearance for Deploy/Stow
#define Z_CLEARANCE_BETWEEN_PROBES  5 // Z Clearance between probe points
#define Z_PROBE_OFFSET_RANGE_MIN -20
#define Z_PROBE_OFFSET_RANGE_MAX 20
#define X_ENABLE_ON 0
#define Y_ENABLE_ON 0
#define Z_ENABLE_ON 0
#define E_ENABLE_ON 0 // For all extruders
#define DISABLE_X true
#define DISABLE_Y true
#define DISABLE_Z false
#define DISABLE_E false // For all extruders
#define DISABLE_INACTIVE_EXTRUDER true // Keep only the active extruder enabled.
#define INVERT_X_DIR true
#define INVERT_Y_DIR true
#define INVERT_Z_DIR true
#define INVERT_E0_DIR true
#define INVERT_E1_DIR false
#define INVERT_E2_DIR false
#define INVERT_E3_DIR false
#define INVERT_E4_DIR false
#define X_HOME_DIR -1
#define Y_HOME_DIR -1
#define Z_HOME_DIR -1
#define X_BED_SIZE 215
#define Y_BED_SIZE 215
#define X_MIN_POS -5
#define Y_MIN_POS 0
#define Z_MIN_POS 0
#define X_MAX_POS X_BED_SIZE
#define Y_MAX_POS Y_BED_SIZE
#define Z_MAX_POS 150
#define MIN_SOFTWARE_ENDSTOPS
  #define MIN_SOFTWARE_ENDSTOP_X
  #define MIN_SOFTWARE_ENDSTOP_Y
  #define MIN_SOFTWARE_ENDSTOP_Z
#define MAX_SOFTWARE_ENDSTOPS
  #define MAX_SOFTWARE_ENDSTOP_X
  #define MAX_SOFTWARE_ENDSTOP_Y
  #define MAX_SOFTWARE_ENDSTOP_Z
#define HOMING_FEEDRATE_XY 2000
#define HOMING_FEEDRATE_Z  400
#define EEPROM_CHITCHAT   // Give feedback on EEPROM commands. Disable to save PROGMEM.
#define HOST_KEEPALIVE_FEATURE        // Disable this if your host doesn't like keepalive messages
#define DEFAULT_KEEPALIVE_INTERVAL 2  // Number of seconds between "busy" messages. Set with M113.
#define BUSY_WHILE_HEATING            // Some hosts require "busy" messages even during heating
#define PREHEAT_1_TEMP_HOTEND 200
#define PREHEAT_1_TEMP_BED    60
#define PREHEAT_1_FAN_SPEED   0 // Value from 0 to 255
#define PREHEAT_2_TEMP_HOTEND 220
#define PREHEAT_2_TEMP_BED    100
#define PREHEAT_2_FAN_SPEED   0 // Value from 0 to 255
#define NOZZLE_PARK_FEATURE
  #define NOZZLE_PARK_POINT { (X_MIN_POS + 10), (Y_MAX_POS - 10), 20 }
  #define NOZZLE_PARK_XY_FEEDRATE 100   // X and Y axes feedrate in mm/s (also used for delta printers Z axis)
  #define NOZZLE_PARK_Z_FEEDRATE 2      // Z axis feedrate in mm/s (not used for delta printers)
#define PRINTJOB_TIMER_AUTOSTART
#define LCD_LANGUAGE en
#define DISPLAY_CHARSET_HD44780 JAPANESE
#define SDSUPPORT
#define REPRAP_DISCOUNT_SMART_CONTROLLER
#define SOFT_PWM_SCALE 0
#define SERVO_DELAY { 300 }

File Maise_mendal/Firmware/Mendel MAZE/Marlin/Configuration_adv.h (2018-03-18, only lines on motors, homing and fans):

#define E0_AUTO_FAN_PIN -1
#define E1_AUTO_FAN_PIN -1
#define E2_AUTO_FAN_PIN -1
#define E3_AUTO_FAN_PIN -1
#define E4_AUTO_FAN_PIN -1
#define X_HOME_BUMP_MM 5
#define Y_HOME_BUMP_MM 5
#define Z_HOME_BUMP_MM 2
#define HOMING_BUMP_DIVISOR { 2, 2, 4 }  // Re-Bump Speed Divisor (Divides the Homing Feedrate)
#define MICROSTEP_MODES {16,16,16,16,16} // [1,2,4,8,16]
#define DIGIPOT_I2C_MOTOR_CURRENTS { 1.0, 1.0, 1.0, 1.0, 1.0, 1.0, 1.0, 1.0 }  //  AZTEEG_X3_PRO
#define ADVANCED_PAUSE_FEATURE
  #define ADVANCED_PAUSE_EXTRUDE_FEEDRATE 3   // Extrude filament feedrate in mm/s - must be slower than load feedrate
  #define ADVANCED_PAUSE_EXTRUDE_LENGTH 100    // Extrude filament length in mm after filament is loaded over the hotend,

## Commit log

2016-05-14 INICIO Tenho a necessidade de reordenar todos os documentos dentro deste fork. Nas proximas etapas vou actualizar e criar o sistema de pastas que vou usar para este projecto.
    [bar-clamp.scad, bar-clamp.stl, bearing-guide.scad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]
2017-01-09 Beta
    Blender Files stars assenbley
    [Maise-Mendel-Plate-4_002.stl, Maise.blend, Y_axes-PAD_mesa.stl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]
2018-01-24 Carrinho X
    [Corte e Furação base.3dm, Corte e Furação base.dxf, endStop.blend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]
2018-02-15 version X beta
    version X beta
    [40mmFan.stl, Maise-000_FIXA__O_Z_STEEPER.stl, Maise-000_SUPORT_ESTRUTURA_COMPRIDO_001.stl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]
2018-03-03 temp
    temp
    [Maise-000_FIXA__O_Z_STEEPER.stl, Maise-000_Suporte_X.stl, Maise-000_Y_motor_Mendel_BASE.stl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]
2018-03-10 A LOT
    Config, marlin base of hephestos,
    Had a lot of features on the machine that is in beta fase!
    A lot more will be done in the next fiew days
    [40mmFan.stl, BASE_CUT_WOOD.3dm, BASE_CUT_WOOD.DXF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]
2018-03-18 Update
    Names of parts updated X Y axis
    Remove old STLS parts, new ones have to be created!
    [Configuration.h, Configuration_adv.h, MKS_GEN1.4Board.blend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]
2018-03-20 updates
    updates
    [Maise-calibration_cube.stl]
2018-03-20 update
    updating instructions
    [BASE_CUT_WOOD.3dm, BASE_CUT_WOOD.DXF]
2018-03-20 updated
    updated
    [BASE_CUT_WOOD.3dm, Maise-002_X_carruage.stl, Maise-calibration_cube.stl]
2018-03-21 update
    update
    [BASE_CUT_WOOD.3dm]
2018-04-05 updated
    marlin firmware updated steps per mm
    [Configuration.h, Maise-001_-_glass_guide.stl, Maise-001_-_glass_guide_001.stl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]

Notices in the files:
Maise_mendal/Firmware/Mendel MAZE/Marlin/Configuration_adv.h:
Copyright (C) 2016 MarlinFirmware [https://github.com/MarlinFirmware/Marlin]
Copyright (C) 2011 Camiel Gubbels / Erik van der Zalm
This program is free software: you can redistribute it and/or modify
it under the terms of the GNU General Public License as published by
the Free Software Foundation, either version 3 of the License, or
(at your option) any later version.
